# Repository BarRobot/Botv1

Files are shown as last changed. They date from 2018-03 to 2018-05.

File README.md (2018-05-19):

# Botv1
BarRobot is a South African design for a Bartending Robot machine.  
It comes with a really easy to use user interface: Selector Switch to choose Single, Double.  And one big red illuminited "Go" button.  Can't be easier!
WS2812B LEDs surround the spirits bottle, helping to invite friends closer - attracted by RGB Blinkies!

## Electronics:
This is a render of the Version 1 Electronics Pack 

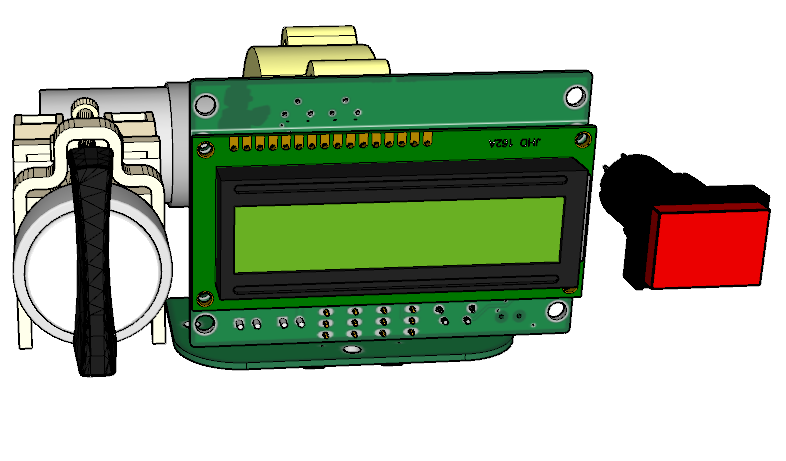
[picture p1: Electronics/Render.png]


## Mascot! 

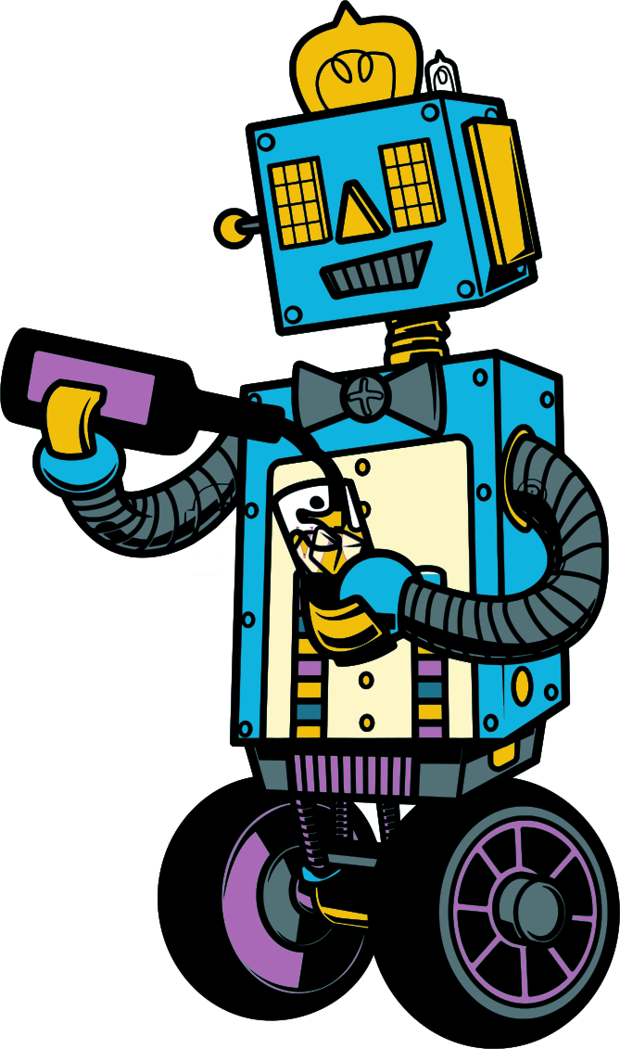
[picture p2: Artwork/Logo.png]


This is our official Mascot, designed by the talented [LUISDJT](https://www.fiverr.com/luisdjt) - Thanks for the cool Mascot!

## Early prototypes in action

Here's an old version, in use:

IMAGE ALT TEXT HERE (https://youtu.be/pBehmayH-3A)

(Youtube Link)

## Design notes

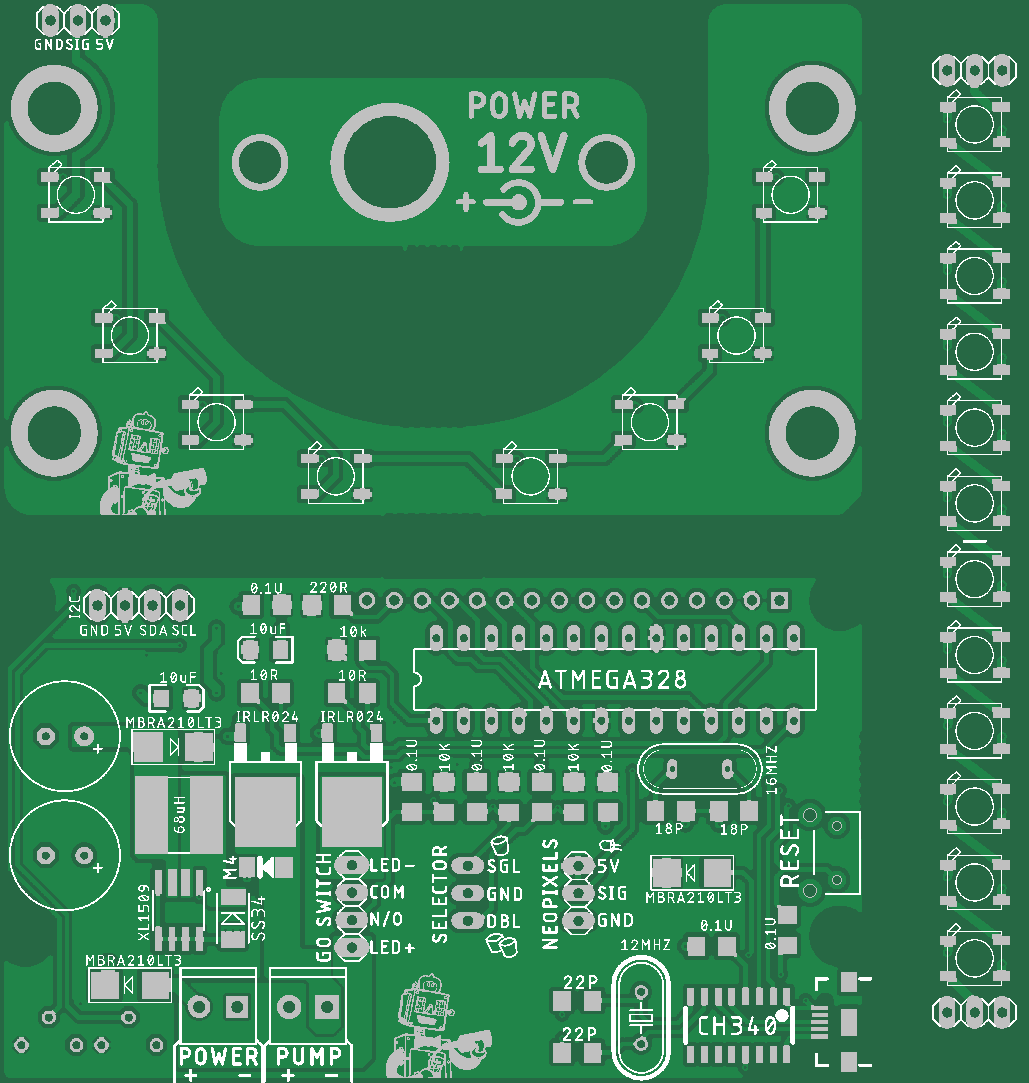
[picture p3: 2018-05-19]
Electronics/eagleUp/eagleUp_BARBOT_board_top.png

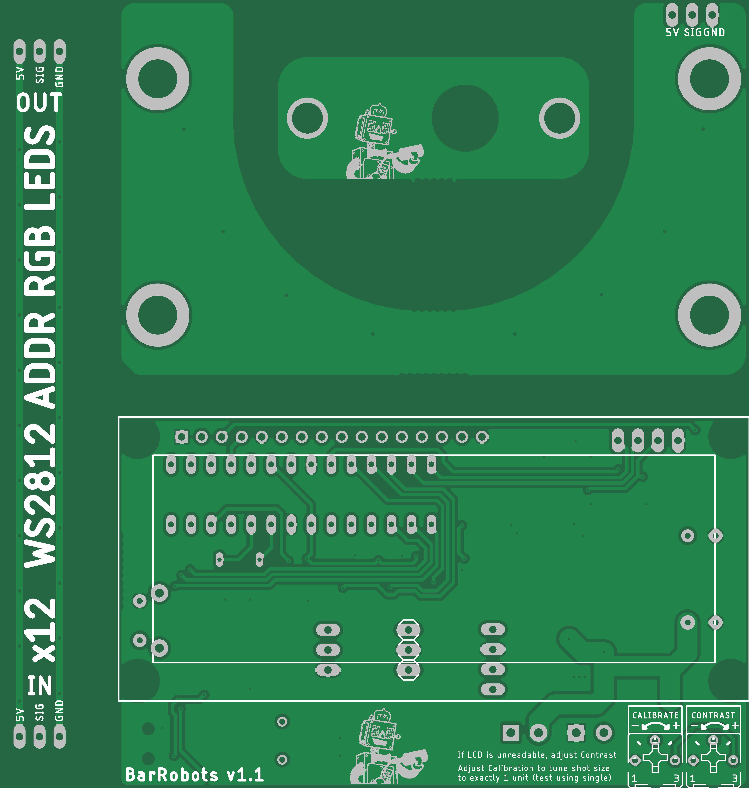
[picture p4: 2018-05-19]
Electronics/eagleUp/eagleUp_BARBOT_board_bottom.png

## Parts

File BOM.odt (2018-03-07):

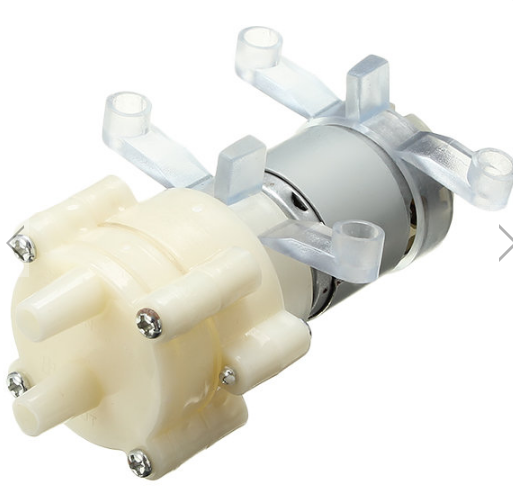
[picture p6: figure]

6-12v RS385 Water Pump https://www.banggood.com/12V-DC-Diaphragm-Pump-Water-Device-Mini-Self-priming-Pump-Fish-Tank-Motor-p-1078807.html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 | | QTY: 10 pc

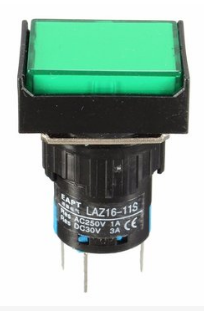
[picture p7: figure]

Switch: 16mm body, 19x24mm rectangle, MOMENTARY, 12V (Similar to https://www.banggood.com/16mm-DC-12V-Push-Button-Self-Lock-Switch-Square-LED-Light-Momentary-Button-p-1002462.html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 but MOMENTARY NB) | | QTY: 20 pc GREEN MOMENTARY QTY: 20 pc RED MOMENTARY QTY: 20 pc AMBER MOMENTARY

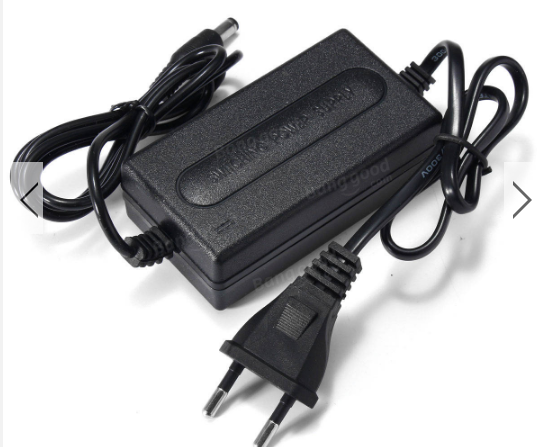
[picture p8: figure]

12V 2A power Supply EU Plug 2.1mm x 5.5mm Plug https://www.banggood.com/AC-110-240V-To-DC-12V-2A-Power-Supply-Transformer-EUUK-LED-Strip-Light-Belt-Adapter-p-1166863.html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 | | QTY: 10 pc 220/240v->12v 2A

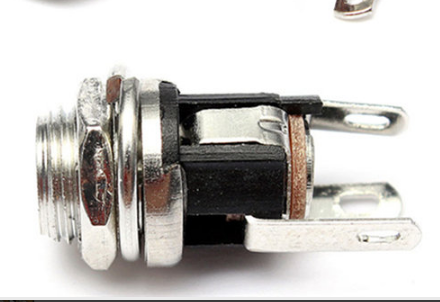
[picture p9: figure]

2.1mm x 5.5mm Socket – Panel Mount (Matching socket for PSU above) https://www.banggood.com/10Pcs-5_5mm-x-2_1mm-DC-Power-Supply-Metal-Jack-Socket-With-Nut-And-Washer-p-1063885.html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 | | QTY: 10pc

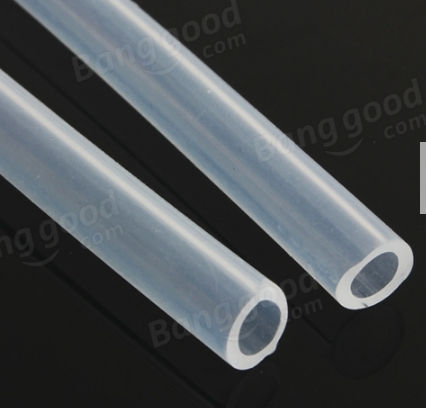
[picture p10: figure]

8MM ID Silicon tubing (for use with the pump above) | | QTY: 15 meter

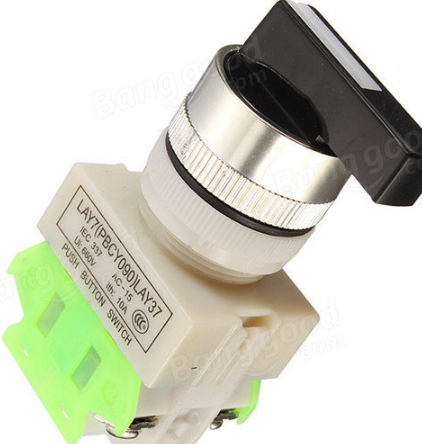
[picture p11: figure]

3 position selector switch https://www.banggood.com/Rotary-Three-Position-Selector-Switch-Push-Button-Switch-p-1126181.html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 | | QTY: 10 pc

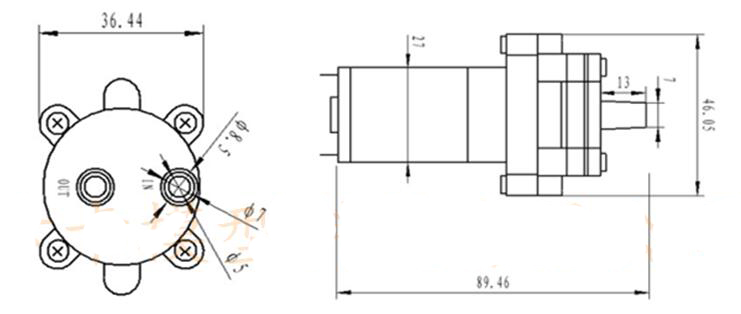
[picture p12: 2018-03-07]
Components/Pump/385-DC-6V-12V-high-temperature-resistance-100-degrees-Celsius-Micro-Pump-diaphragm-water-pump-vacuum.jpg

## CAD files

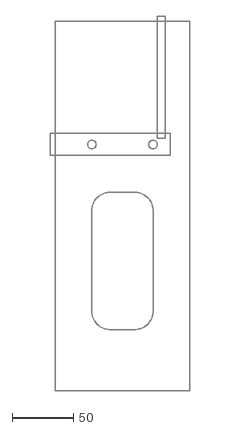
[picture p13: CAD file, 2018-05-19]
Chassis/DXF/panel2.dxf
114.0 x 306.0

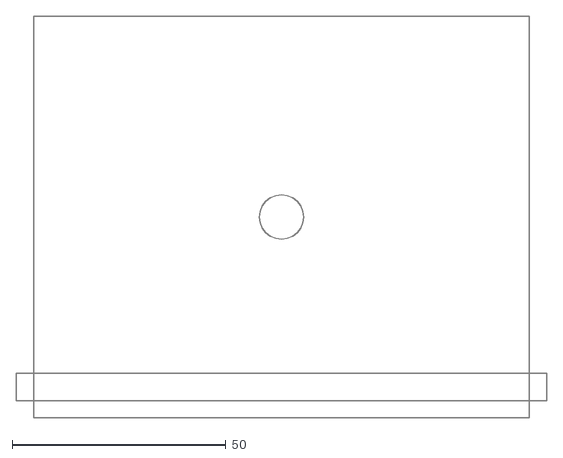
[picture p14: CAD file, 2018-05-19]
Chassis/DXF/panel6.dxf
124.0 x 94.0

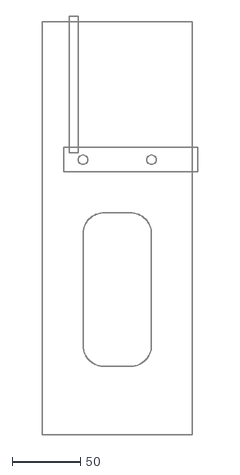
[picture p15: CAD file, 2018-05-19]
Chassis/DXF/panel1.dxf
114.0 x 306.0

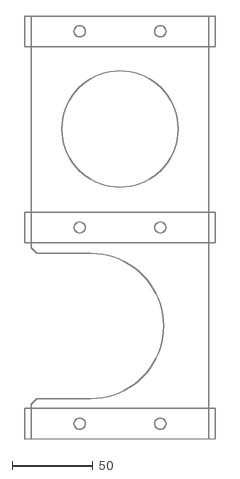
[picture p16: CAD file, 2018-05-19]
Chassis/DXF/panel4.dxf
118.0 x 262.0

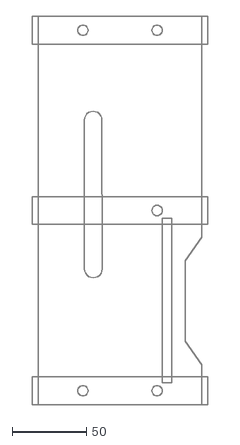
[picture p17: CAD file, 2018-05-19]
Chassis/DXF/panel5.dxf
118.0 x 262.0

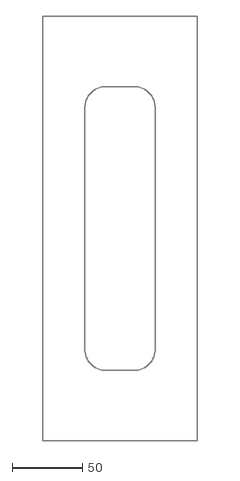
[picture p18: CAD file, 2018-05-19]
Chassis/DXF/panel3.dxf
110.0 x 302.0

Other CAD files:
Components/Pump/RS385-Water-Pump.skp
Components/Selector Switch.skp

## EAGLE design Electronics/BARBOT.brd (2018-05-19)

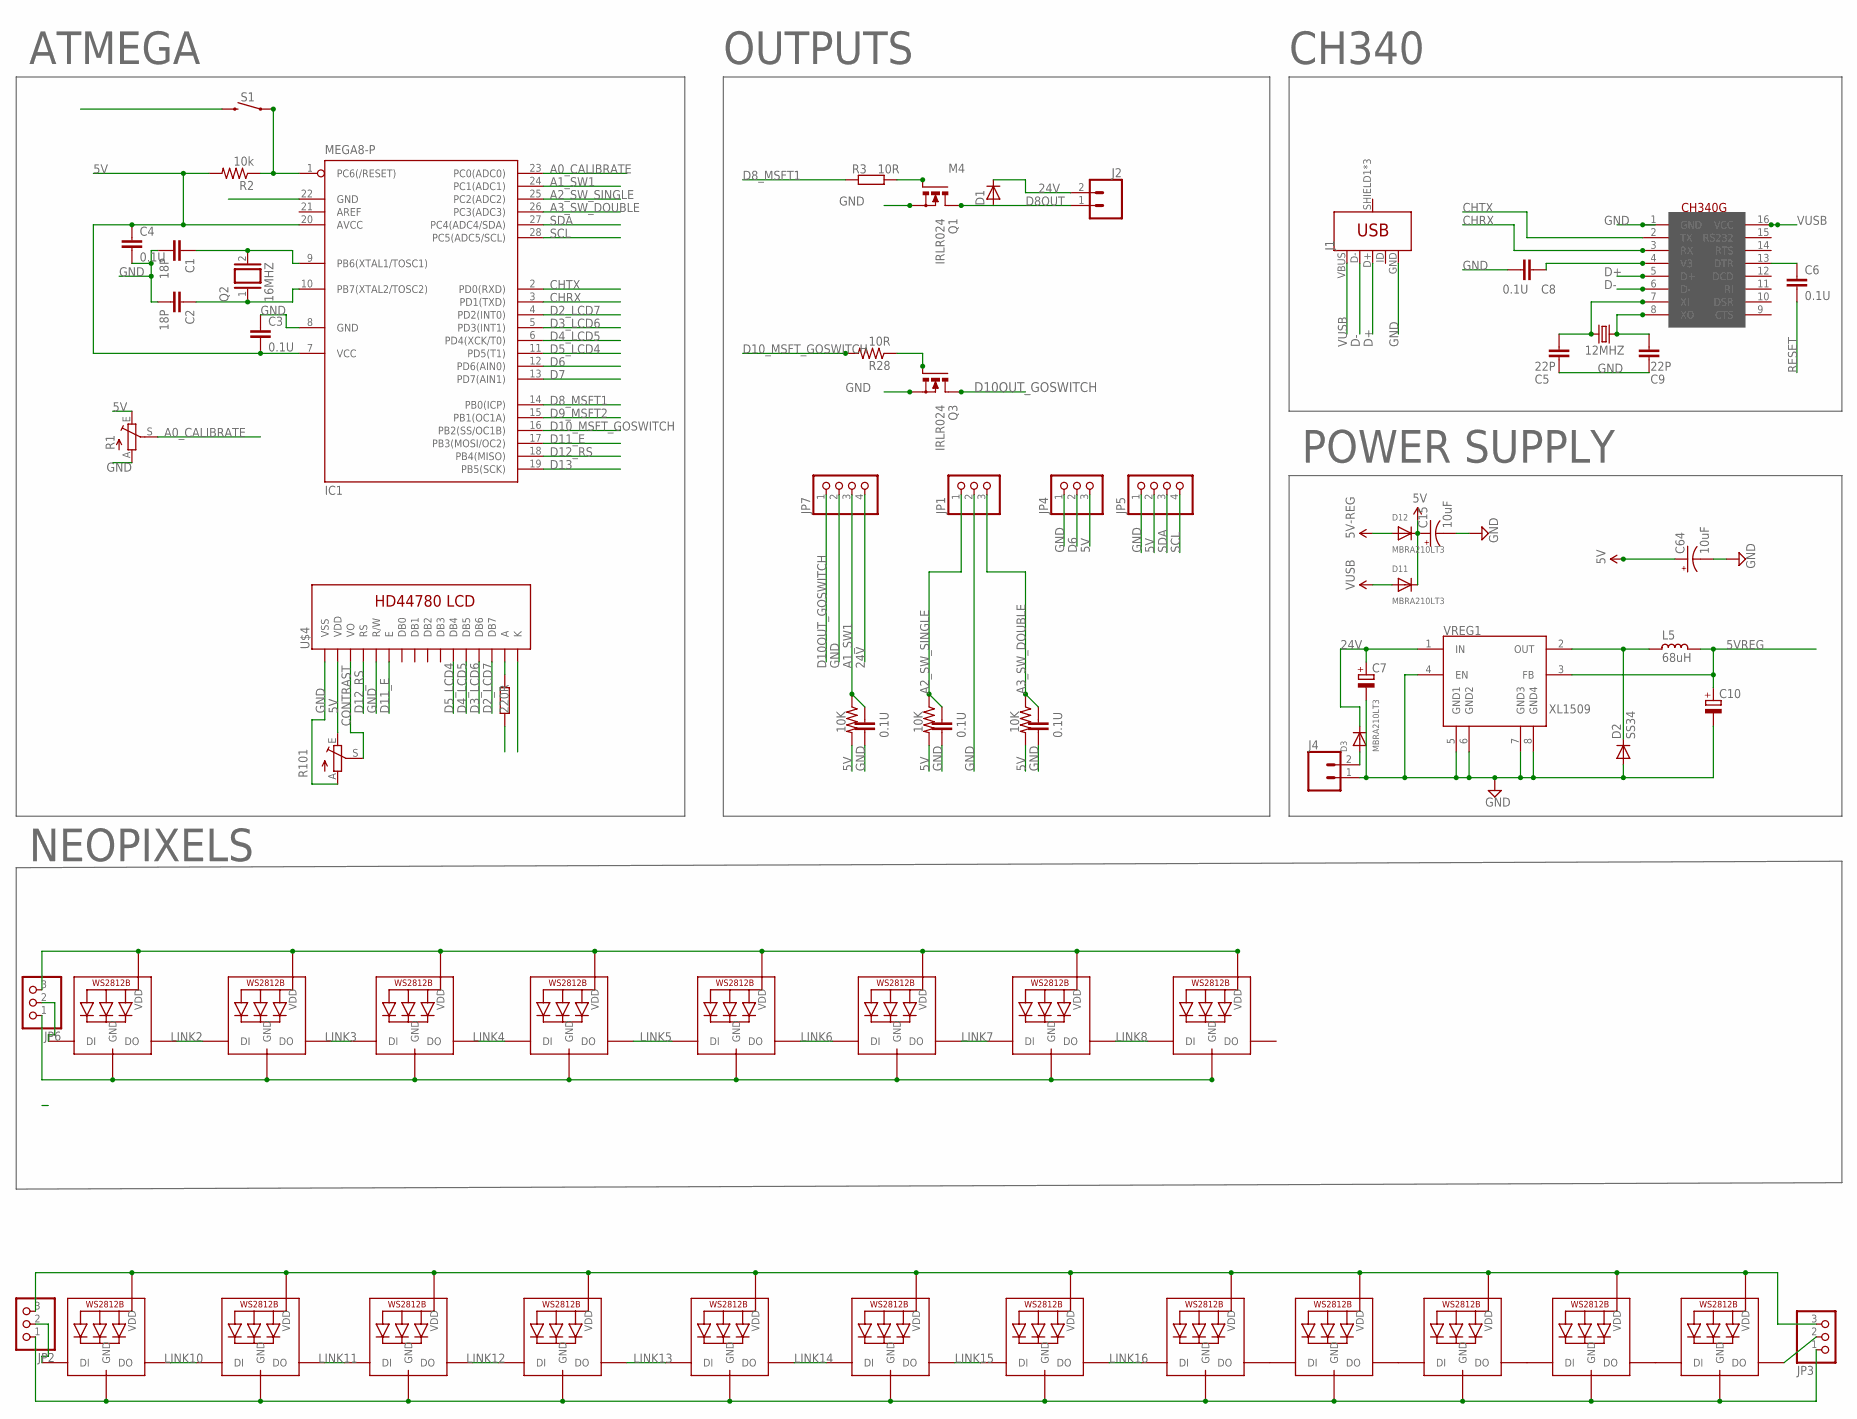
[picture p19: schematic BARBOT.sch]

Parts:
12MHZ: 12MHZ; HC49U70
C1, C2: 18P; C1206
C3, C4, C6, C8, C11, C12, C13: 0.1U; C1206
C5, C9: 22P; C1206
C7, C10: CPOL-EUE3.5-10; E3,5-10
C15, C64: 10uF; EIA3216
D1: M4; SOD80
D2: SS34; DO-214AC
D3, D11, D12: MBRA210LT3; SMADIODE
IC1: MEGA8-P; DIL28-3
J1: USB_MICRO-BREDUCED_PASTE; USB-B-MICRO-SMD_RED_PASTE
J2, J4: CONN_023.5MM; SCREWTERMINAL-3.5MM-2
JP1, JP2, JP3, JP4, JP6: PINHD-1X3; 1X03
JP5, JP7: PINHD-1X4; 1X04
L5: 68uH; CD75
LED1, LED2, LED3, LED4, LED5, LED6, LED7, LED8, LED9, LED10, LED11, LED12, LED13, LED14, LED15, LED16, LED17, LED18, LED19, LED20: WS2812B5050; WS2812B
Q1, Q3: IRLR024; D-PAK_TO252AA
Q2: 16MHZ; QS
R1, R101: TRIM_EU-B25P; B25P
R2: 10k; R1206
R3: 10R; R1206
R4: 220R; R1206
R5, R6, R7: 10K; R1206@1
R28: 10R; R1206@1
S1: MOMENTARY-SWITCH-SPST-PTH-RIGHT-ANGLE-KIT; TACTILE_SWITCH_PTH_RIGHT_ANGLE_KIT
U$2: CH340G; SOIC16
U$4: LCD-HD447804-HOLES16X2-4-HOLES; LCD-16X2-4HOLES
VREG1: XL1509; SO08

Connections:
5V: C3.2, C4.1, C15.A (+), C64.A (+), D11.C, D12.C, IC1.7 (VCC), IC1.20 (AVCC), JP4.3, JP5.2, JP6.3, LED1.1-VDD (VDD), LED2.1-VDD (VDD), LED3.1-VDD (VDD), LED4.1-VDD (VDD), LED5.1-VDD (VDD), LED6.1-VDD (VDD), LED7.1-VDD (VDD), LED8.1-VDD (VDD), R1.E, R2.2, R4.1, R5.2, R6.2, R7.2, R101.E, U$4.2 (VDD)
5V1: JP2.3, JP3.3, LED9.1-VDD (VDD), LED10.1-VDD (VDD), LED11.1-VDD (VDD), LED12.1-VDD (VDD), LED13.1-VDD (VDD), LED14.1-VDD (VDD), LED15.1-VDD (VDD), LED16.1-VDD (VDD), LED17.1-VDD (VDD), LED18.1-VDD (VDD), LED19.1-VDD (VDD), LED20.1-VDD (VDD)
5VREG: C10.+, D12.A, L5.1, VREG1.3 (FB)
24V: C7.+, D1.1 (C), D3.C, J2.2, JP7.4, VREG1.1 (IN)
A0_CALIBRATE: IC1.23 (PC0(ADC0)), R1.S
A1_SW1: C11.1, IC1.24 (PC1(ADC1)), JP7.3, R5.1
A2_SW_SINGLE: C12.1, IC1.25 (PC2(ADC2)), JP1.1, R6.1
A3_SW_DOUBLE: C13.1, IC1.26 (PC3(ADC3)), JP1.3, R7.1
CHRX: IC1.3 (PD1(TXD)), U$2.3 (RX)
CHTX: IC1.2 (PD0(RXD)), U$2.2 (TX)
CONTRAST: R101.S, U$4.3 (VO)
D2_LCD7: IC1.4 (PD2(INT0)), U$4.14 (DB7)
D3_LCD6: IC1.5 (PD3(INT1)), U$4.13 (DB6)
D4_LCD5: IC1.6 (PD4(XCK/T0)), U$4.12 (DB5)
D5_LCD4: IC1.11 (PD5(T1)), U$4.11 (DB4)
D6: IC1.12 (PD6(AIN0)), JP4.2
D7: IC1.13 (PD7(AIN1))
D8OUT: D1.2 (A), J2.1, Q1.4 (D)
D8_MSFT1: IC1.14 (PB0(ICP)), R3.1
D9_MSFT2: IC1.15 (PB1(OC1A))
D10OUT_GOSWITCH: JP7.1, Q3.4 (D)
D10_MSFT_GOSWITCH: IC1.16 (PB2(SS/OC1B)), R28.2
D11_E: IC1.17 (PB3(MOSI/OC2)), U$4.6 (E)
D12_RS: IC1.18 (PB4(MISO)), U$4.4 (RS)
D13: IC1.19 (PB5(SCK))
D+: J1.D+, U$2.5 (D+)
D-: J1.D-, U$2.6 (D-)
GND: C1.2, C2.2, C3.1, C4.2, C5.2, C7.-, C8.2, C9.2, C10.-, C11.2, C12.2, C13.2, C15.C (-), C64.C (-), D2.2 (A), IC1.8 (GND), IC1.22 (GND), J1.GND, J4.1, JP1.2, JP4.1, JP5.1, JP6.1, JP7.2, LED1.3-GND (GND), LED2.3-GND (GND), LED3.3-GND (GND), LED4.3-GND (GND), LED5.3-GND (GND), LED6.3-GND (GND), LED7.3-GND (GND), LED8.3-GND (GND), Q1.3 (S), Q3.3 (S), R1.A, R101.A, S1.2, U$2.1 (GND), U$4.1 (VSS), U$4.5 (R/W), U$4.16 (K), VREG1.4 (EN), VREG1.5 (GND1), VREG1.6 (GND2), VREG1.7 (GND3), VREG1.8 (GND4)
GND1: JP2.1, JP3.1, LED9.3-GND (GND), LED10.3-GND (GND), LED11.3-GND (GND), LED12.3-GND (GND), LED13.3-GND (GND), LED14.3-GND (GND), LED15.3-GND (GND), LED16.3-GND (GND), LED17.3-GND (GND), LED18.3-GND (GND), LED19.3-GND (GND), LED20.3-GND (GND)
LINK1: JP6.2, LED1.4-DIN (DI)
LINK2: LED1.2-DOUT (DO), LED2.4-DIN (DI)
LINK3: LED2.2-DOUT (DO), LED3.4-DIN (DI)
LINK4: LED3.2-DOUT (DO), LED4.4-DIN (DI)
LINK5: LED4.2-DOUT (DO), LED5.4-DIN (DI)
LINK6: LED5.2-DOUT (DO), LED6.4-DIN (DI)
LINK7: LED6.2-DOUT (DO), LED7.4-DIN (DI)
LINK8: LED7.2-DOUT (DO), LED8.4-DIN (DI)
LINK9: JP2.2, LED9.4-DIN (DI)
LINK10: LED9.2-DOUT (DO), LED10.4-DIN (DI)
LINK11: LED10.2-DOUT (DO), LED11.4-DIN (DI)
LINK12: LED11.2-DOUT (DO), LED12.4-DIN (DI)
LINK13: LED12.2-DOUT (DO), LED13.4-DIN (DI)
LINK14: LED13.2-DOUT (DO), LED14.4-DIN (DI)
LINK15: LED14.2-DOUT (DO), LED15.4-DIN (DI)
LINK16: LED15.2-DOUT (DO), LED16.4-DIN (DI)
unnamed: Q1.1 (G), R3.2
unnamed: C6.1, U$2.13 (DTR)
unnamed: C1.1, IC1.9 (PB6(XTAL1/TOSC1)), Q2.2
unnamed: D3.A, J4.2
unnamed: C2.1, IC1.10 (PB7(XTAL2/TOSC2)), Q2.1
unnamed: JP3.2, LED20.2-DOUT (DO)
unnamed: LED16.2-DOUT (DO), LED17.4-DIN (DI)
unnamed: LED17.2-DOUT (DO), LED18.4-DIN (DI)
unnamed: 12MHZ.1, C5.1, U$2.7 (XI)
unnamed: R4.2, U$4.15 (A)
unnamed: 12MHZ.2, C9.1, U$2.8 (XO)
unnamed: C8.1, U$2.4 (V3)
unnamed: LED18.2-DOUT (DO), LED19.4-DIN (DI)
unnamed: LED19.2-DOUT (DO), LED20.4-DIN (DI)
unnamed: Q3.1 (G), R28.1
unnamed: D2.1 (C), L5.2, VREG1.2 (OUT)
RESET: C6.2, IC1.1 (PC6(/RESET)), R2.1, S1.1
SCL: IC1.28 (PC5(ADC5/SCL)), JP5.4
SDA: IC1.27 (PC4(ADC4/SDA)), JP5.3
VUSB: D11.A, J1.VBUS, U$2.16 (VCC)

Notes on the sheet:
POWER SUPPLY
OUTPUTS
ATMEGA
CH340
NEOPIXELS

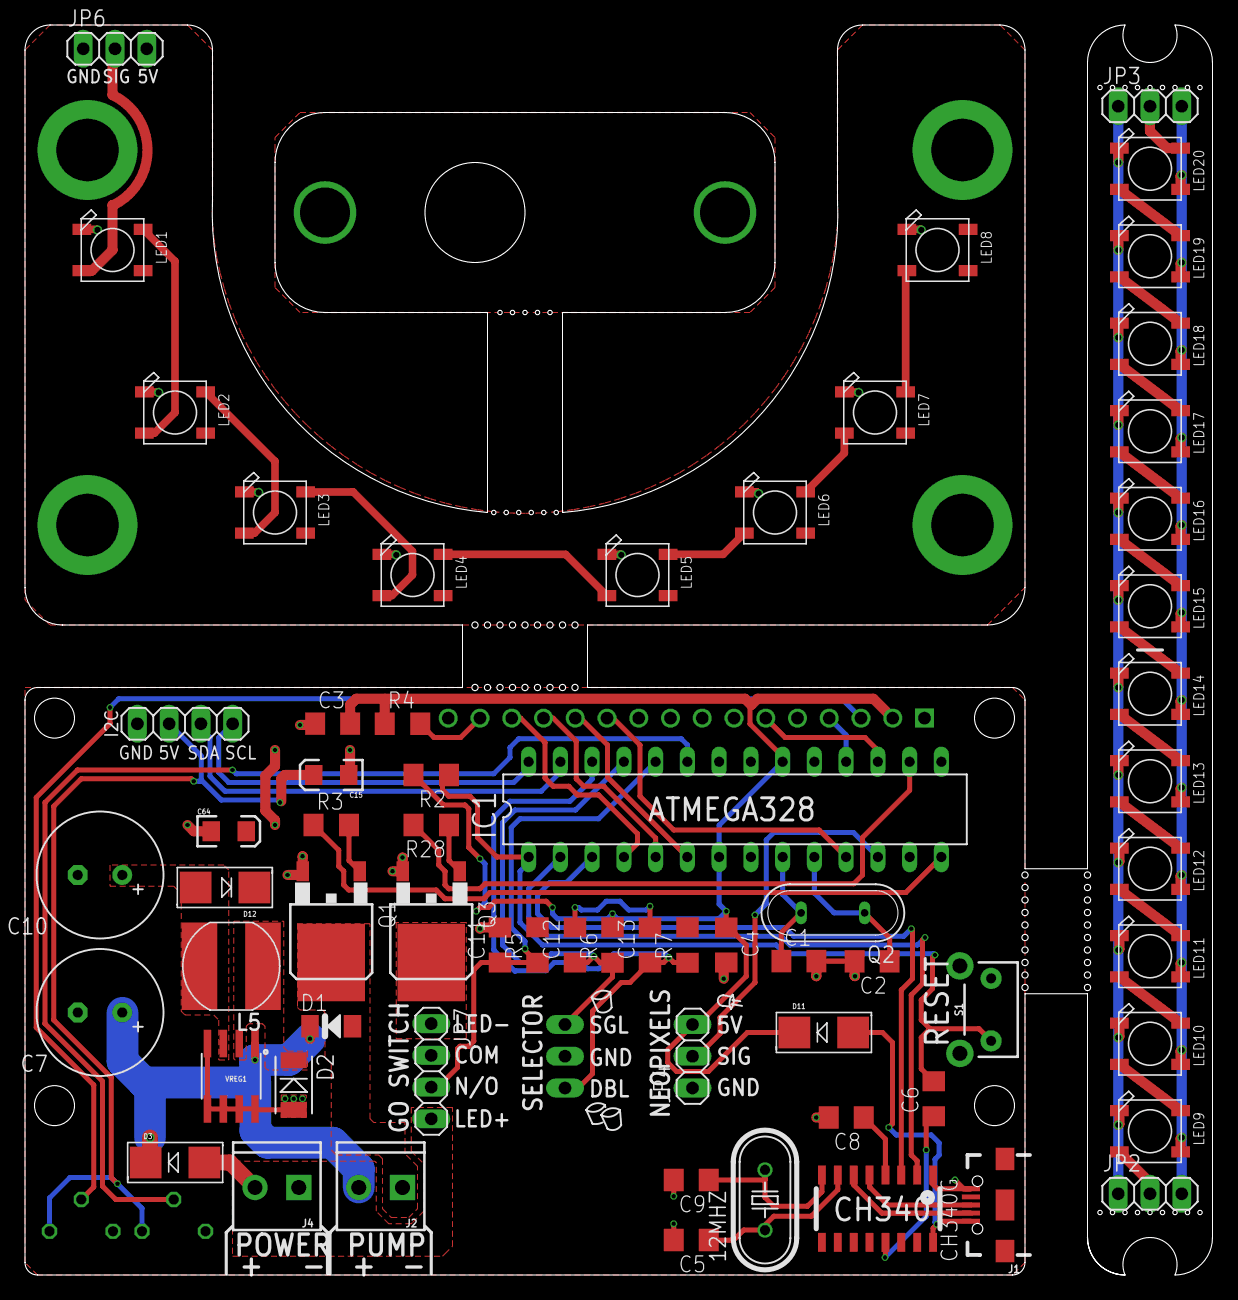
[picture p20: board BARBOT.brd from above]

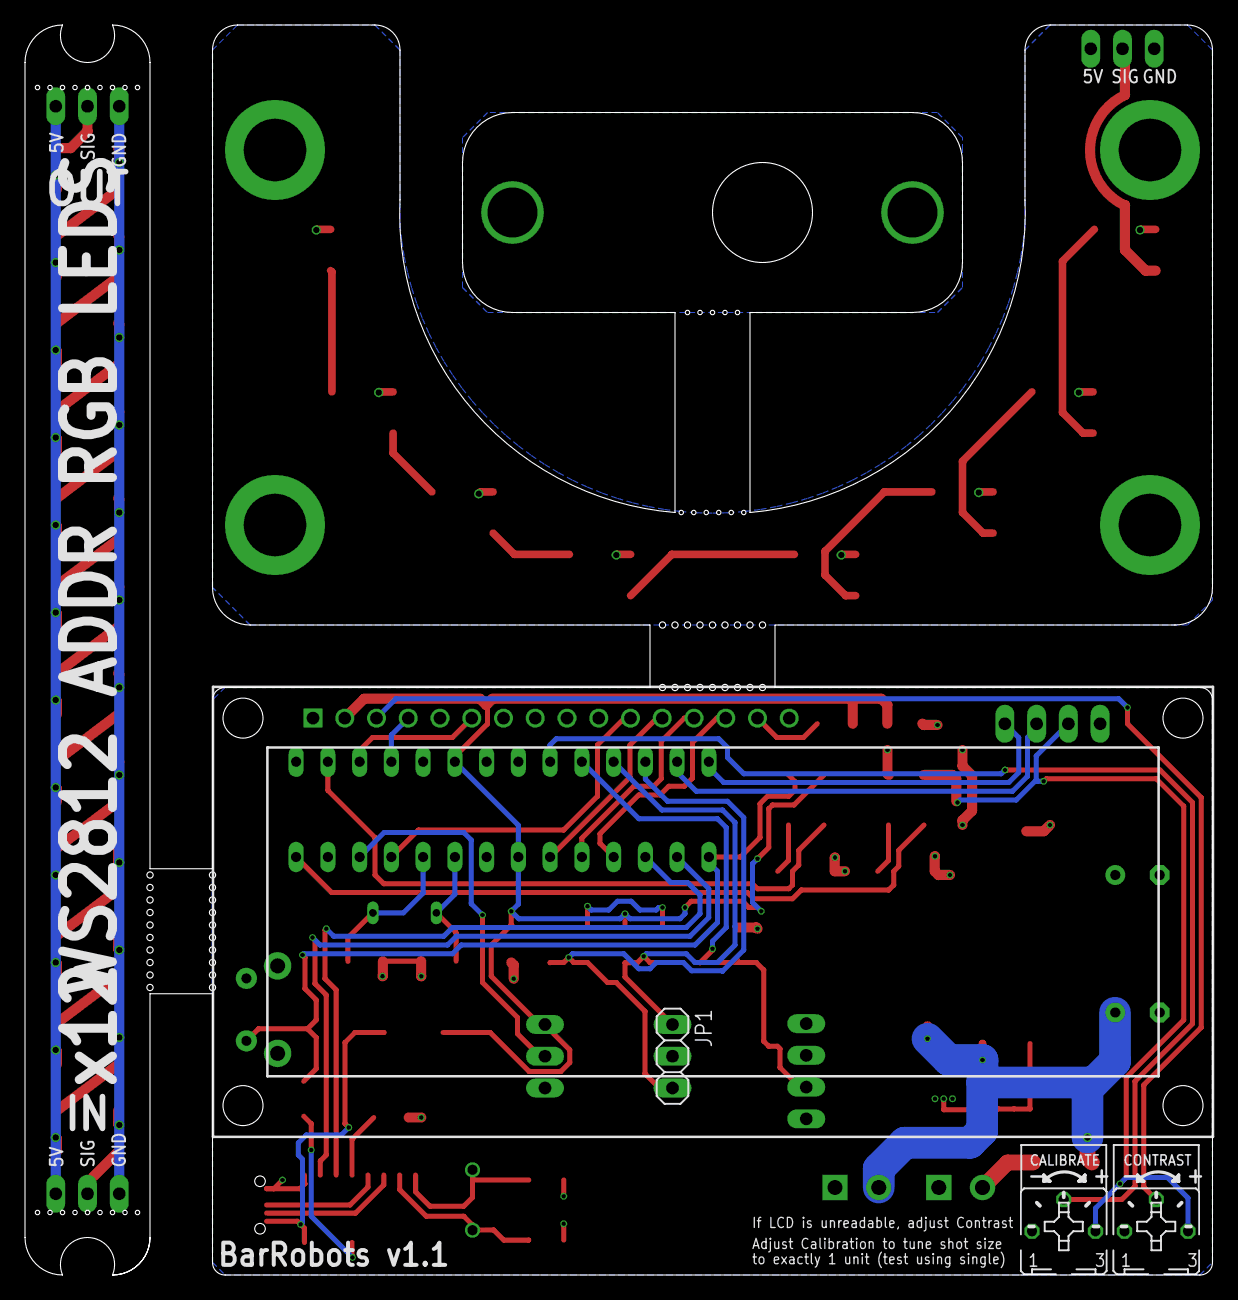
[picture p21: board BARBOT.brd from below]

Board: 2 copper layers, 95.0 x 100.0 mm, 69 parts (4 on the bottom side), 62 nets.

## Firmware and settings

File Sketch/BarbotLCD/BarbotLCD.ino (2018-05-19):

// Barbot LCD
#include <LiquidCrystal.h>
LiquidCrystal lcd(12, 11, 5, 4, 3, 2);

//Barbot Pins
int pixelpin = 6;

#include <Button.h>
// Buttons
//int sglbtn = A1;
//int dblbtn = A2;
//int gobtn = A3;
Button sglbtn(A1); // Connect your button between pin 2 and GND
Button dblbtn(A2); // Connect your button between pin 3 and GND
Button gobtn(A3); // Connect your button between pin 4 and GND


// Transistor Outputs
int pumpswitch = 8;
int sglswitch = 9;
int dblswitch = 10;
int goswitch = 13;


// Neopixels
#include <Adafruit_NeoPixel.h>
#ifdef __AVR__
  #include <avr/power.h>
#endif
#define PIN 6
Adafruit_NeoPixel strip = Adafruit_NeoPixel(8, PIN, NEO_GRB + NEO_KHZ800);


byte p20[8] = {
  B10000,
  B10000,
  B10000,
  B10000,
  B10000,
  B10000,
  B10000,
};
byte p40[8] = {
  B11000,
  B11000,
  B11000,
  B11000,
  B11000,
  B11000,
  B11000,
};
byte p60[8] = {
  B11100,
  B11100,
  B11100,
  B11100,
  B11100,
  B11100,
  B11100,
};
byte p80[8] = {
  B11110,
  B11110,
  B11110,
  B11110,
  B11110,
  B11110,
  B11110,
};
byte p100[8] = {
  B11111,
  B11111,
  B11111,
  B11111,
  B11111,
  B11111,
  B11111,
};

int ledState = LOW;             // ledState used to set the LED
unsigned long previousMillis = 0;        // will store last time LED was updated
const long interval = 100;           // 

void setup() {
  // set up the LCD's number of columns and rows:
  lcd.begin(16, 2);
  lcd.clear();
  // Print a message to the LCD.
  lcd.print("Starting...");
  lcd.createChar(0, p20);
  lcd.createChar(1, p40);
  lcd.createChar(2, p60);
  lcd.createChar(3, p80);
  lcd.createChar(4, p100);
  sglbtn.begin();
  dblbtn.begin();
  gobtn.begin();
  pinMode(pumpswitch, OUTPUT);
  pinMode(sglswitch, OUTPUT);
  pinMode(dblswitch, OUTPUT);
  pinMode(goswitch, OUTPUT);
  strip.begin();
  strip.show(); // Initialize all pixels to 'off'
  digitalWrite(goswitch, HIGH);
  delay(200);
  colorWipe(strip.Color(255, 0, 0), 50); // Red
  digitalWrite(goswitch, LOW);
  colorWipe(strip.Color(0, 255, 0), 50); // Red

  showIdle();
}

void loop() {
  for(int j=0; j<256; j++) { // 5 cycles of all colors on wheel
    for(int i=0; i< strip.numPixels(); i++) {
      strip.setPixelColor(i, Wheel(((i * 256 / strip.numPixels()) + j) & 255));
    }
    strip.show();
    if (gobtn.pressed()) {
      pour();
    }
    if (sglbtn.toggled() || dblbtn.toggled()) {
      showIdle();  
    }
    delay(20);
  }
  
}


void pour() {
  int calibrationValue = analogRead(A0);
  int time = map(calibrationValue, 0, 1023, 500, 3000);
  if (sglbtn.read() == Button::PRESSED) {
     lcd.clear();
     lcd.print("Pouring Single");
     colorWipe(strip.Color(0, 0, 255), 50); // Red
     dispense(time);
     showIdle();
  } else if (dblbtn.read() == Button::PRESSED) {
     lcd.clear();
     lcd.print("Double 1/2");
     colorWipe(strip.Color(0, 0, 255), 50); // Red
     dispense(time);
     lcd.clear();
     lcd.print("Double 2/2");
     colorWipe(strip.Color(0, 255, 0), 50); // Red
     delay(100);
     colorWipe(strip.Color(0, 0, 255), 50); // Red
     dispense(time);
     colorWipe(strip.Color(0, 255, 0), 50); // Red
     showIdle();
  } else {
    lcd.clear();
    lcd.print("Select first!");
    delay(1000);
    showIdle();
  }
  
}

void dispense(int time) {
  digitalWrite(goswitch, HIGH);
  digitalWrite(pumpswitch, HIGH);
  for (int i = 0; i<16; i++) {
    for (int j=0; j<5; j++) {
      lcd.setCursor(i, 1);   
      lcd.write(j);
      delay(time/80);
      unsigned long currentMillis = millis();
      if (currentMillis - previousMillis >= interval) {
        previousMillis = currentMillis;
        if (ledState == LOW) {
          ledState = HIGH;
        } else {
          ledState = LOW;
        }
        digitalWrite(goswitch, ledState);
      }
    }    
  }
  digitalWrite(pumpswitch, LOW);
}

void showIdle() {
  lcd.clear();
  delay(200);
//  lcd.print("Place glass");
  if (sglbtn.read() == Button::PRESSED) {
     lcd.print("Single");
     lcd.setCursor(0, 1);
     lcd.print("Press GO");
  } else if (dblbtn.read() == Button::PRESSED) {
     lcd.print("Double");
     lcd.setCursor(0, 1);
     lcd.print("Press GO");
  } else {
    lcd.print("Select Single");
    lcd.setCursor(0, 1);
    lcd.print("or Double?");
  } 
}

uint32_t Wheel(byte WheelPos) {
  WheelPos = 255 - WheelPos;
  if(WheelPos < 85) {
    return strip.Color(255 - WheelPos * 3, 0, WheelPos * 3);
  }
  if(WheelPos < 170) {
    WheelPos -= 85;
    return strip.Color(0, WheelPos * 3, 255 - WheelPos * 3);
  }
  WheelPos -= 170;
  return strip.Color(WheelPos * 3, 255 - WheelPos * 3, 0);
}

void colorWipe(uint32_t c, uint8_t wait) {
  for(uint16_t i=0; i<strip.numPixels(); i++) {
    strip.setPixelColor(i, c);
    strip.show();
    delay(wait);
  }
}

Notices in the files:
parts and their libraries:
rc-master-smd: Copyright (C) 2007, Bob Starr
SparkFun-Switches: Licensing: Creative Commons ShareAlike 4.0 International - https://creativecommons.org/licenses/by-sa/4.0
